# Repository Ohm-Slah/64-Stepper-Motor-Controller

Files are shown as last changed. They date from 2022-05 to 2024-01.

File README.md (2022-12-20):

# 64-Stepper-Motor-Controller
Controls an 8x8 array of stepper motors and RGB LED light strips, intended for audio/visual performance of a MIDI-like structure. You can certainly make this project with an FPGA, but I don't have much knowledge of FPGA's, so this project is written in C/C++ with the Arduino library included. Due to the incredible number of I/O, three Teensy microcontrollers are currently implemented, two Teensy 4.0's for I/O drivers (32 motors each), and one Teensy 4.1 for the 'main brain'. 

# Concetual initial design
General layout thoughts for such a large number of stepper motors and how to control them. Revision A is mostly based off of Concept #3.

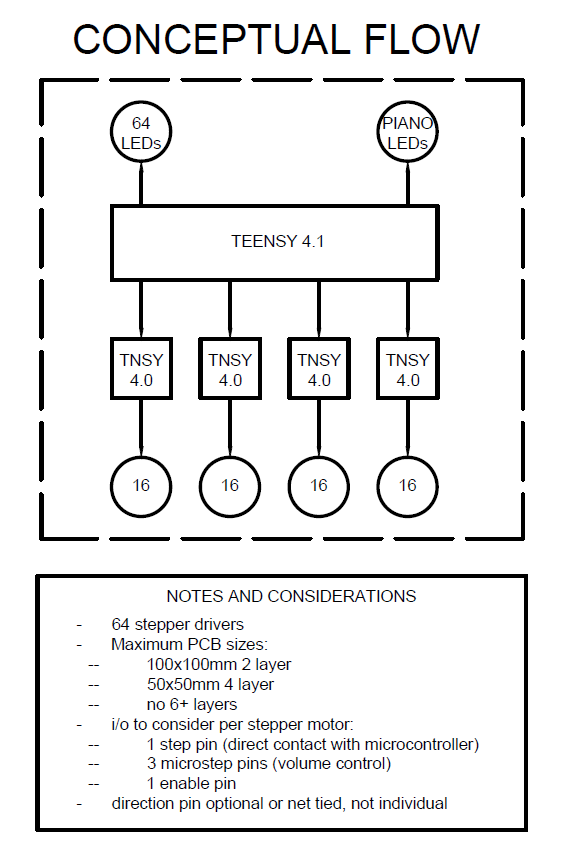
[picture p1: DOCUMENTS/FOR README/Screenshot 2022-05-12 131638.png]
conceptual
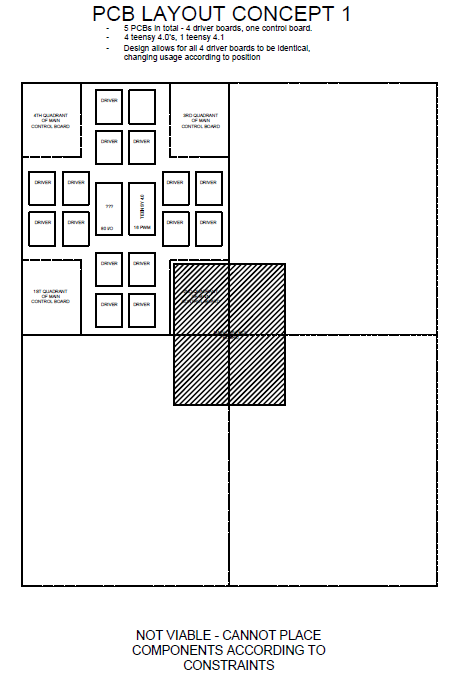
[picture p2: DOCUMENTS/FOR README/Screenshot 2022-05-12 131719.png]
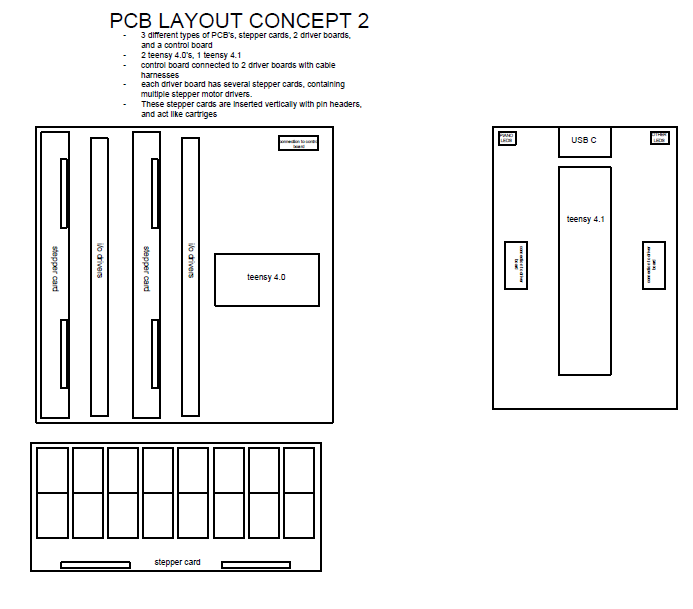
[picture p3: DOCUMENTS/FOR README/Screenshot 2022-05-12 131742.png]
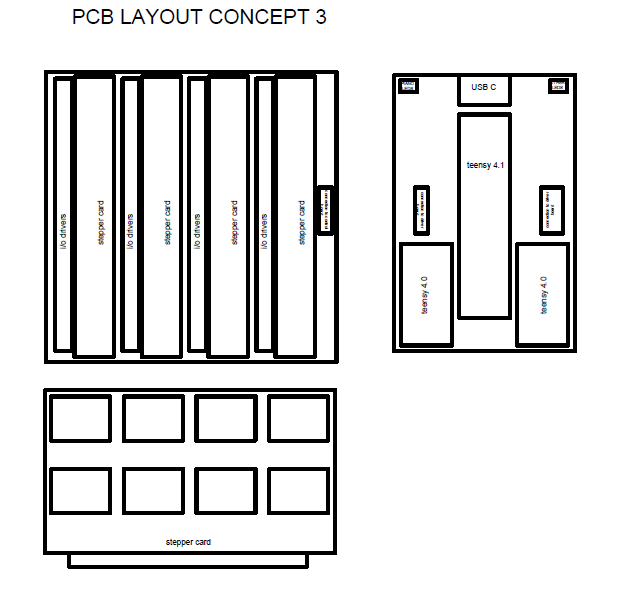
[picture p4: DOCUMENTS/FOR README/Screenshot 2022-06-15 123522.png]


# Revision A
This design is an attempt to create a fairly modular assembly for 64 stepper motor control. Each A4988 stepper driver can be extracted or replaced if neccessary. Eight total A4988 stepper drivers can be placed onto a single driver 'card'. These are designed to be edge-card connected to a larger board, the 32-stepper board. This board holds four driver cards, totalling to 32 stepper motors. There are 2 of these boards to total 64 motor drivers, with each having 20 74HC595 shift registers for I/O management, and visual indicator LED's for all outputs of the shift registers. Power is supplied to this board via a high-current connector. Both of these 32-stepper boards are then connected to a 'main board' containing the 3 microcontrollers, LED strip connections, and USB connection. 

## 8 Stepper PCB Card
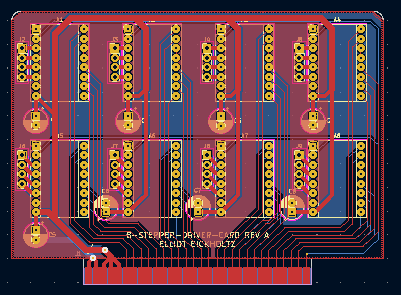
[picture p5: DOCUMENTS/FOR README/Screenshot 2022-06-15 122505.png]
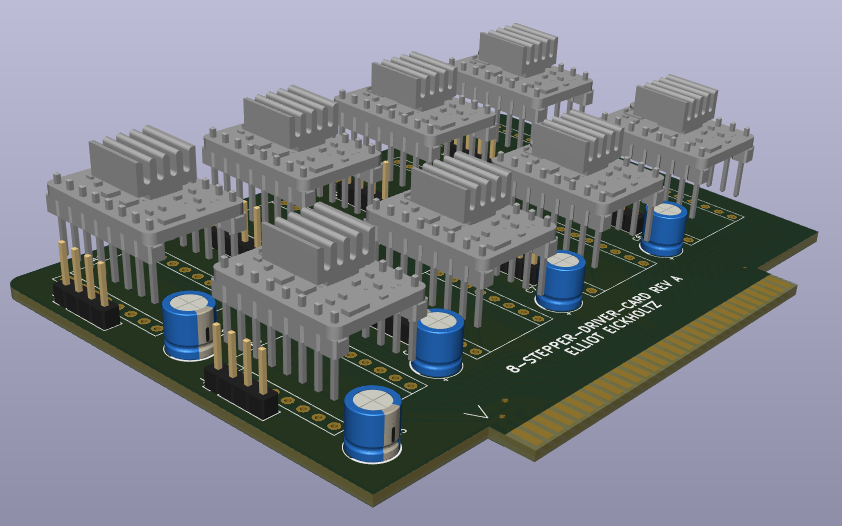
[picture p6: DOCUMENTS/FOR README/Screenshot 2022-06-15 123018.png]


## 32 Stepper PCB Board
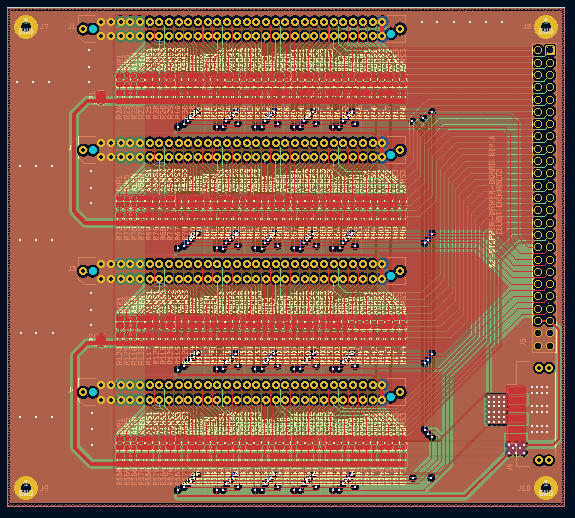
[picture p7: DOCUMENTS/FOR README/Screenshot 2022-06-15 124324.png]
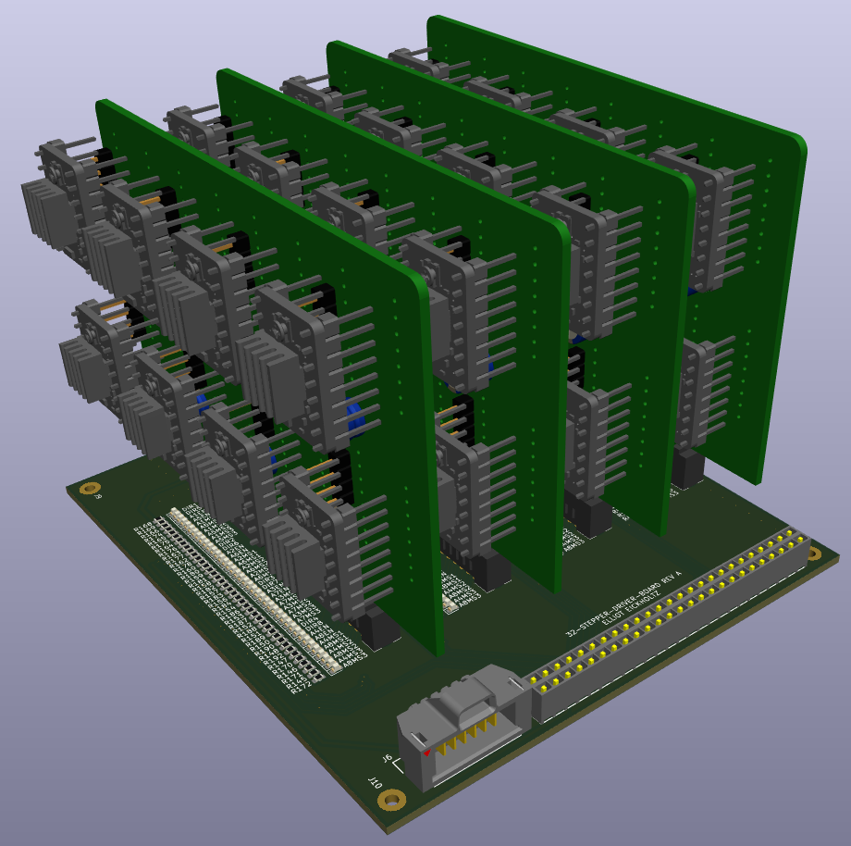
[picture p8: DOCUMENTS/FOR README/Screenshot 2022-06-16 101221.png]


## 64 Stepper PCB Board
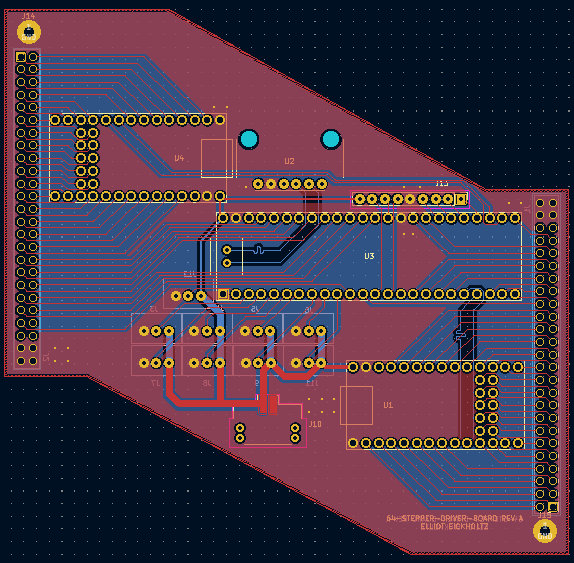
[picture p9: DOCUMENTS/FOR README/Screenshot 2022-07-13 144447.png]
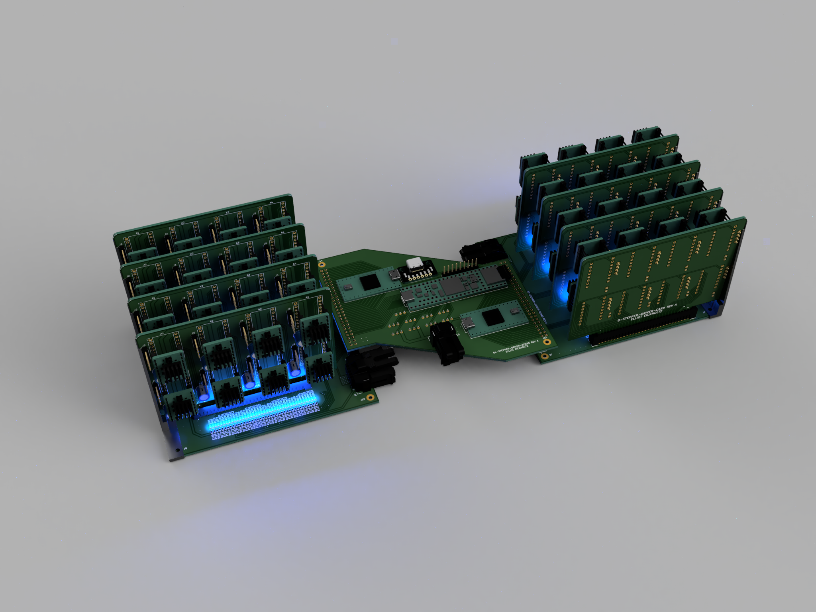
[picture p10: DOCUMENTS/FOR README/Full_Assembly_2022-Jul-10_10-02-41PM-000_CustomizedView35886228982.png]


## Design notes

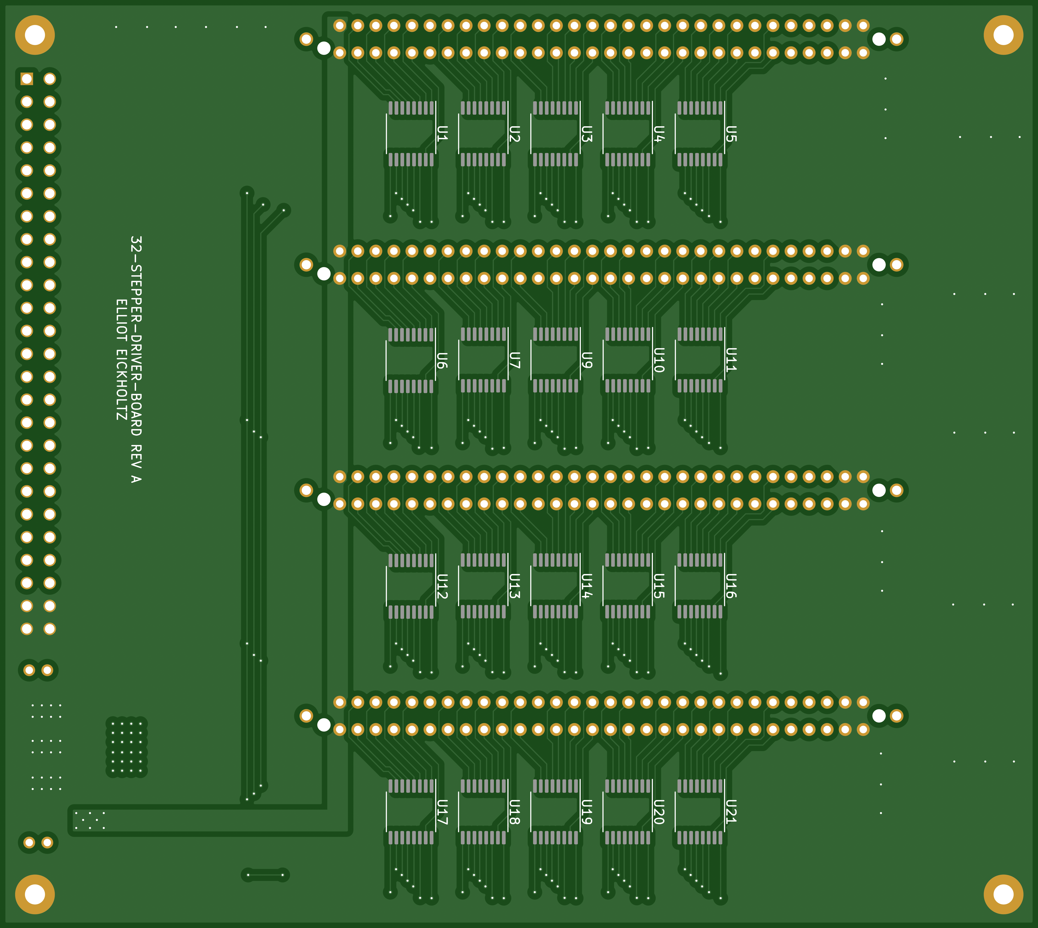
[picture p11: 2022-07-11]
PCB/32-STEPPER-DRIVER-BOARD/SVG/bottom.png

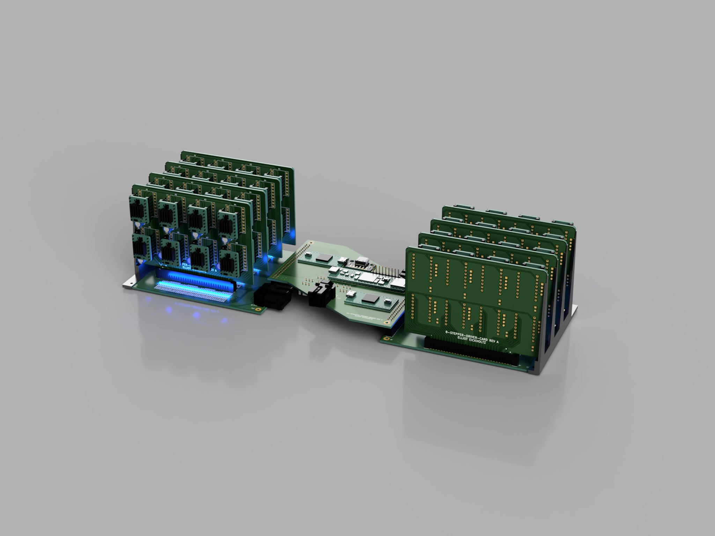
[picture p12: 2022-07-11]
PCB/64-STEPPER-CONTROLLER/32635d5f-a620-4e4e-a5b7-3e85a7bd913b.PNG

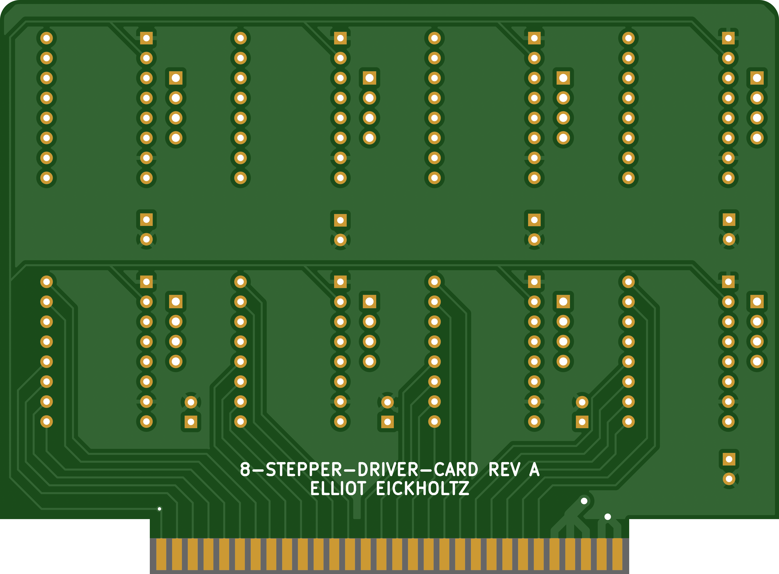
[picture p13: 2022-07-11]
PCB/8-STEPPER-DRIVER-CARD/SVG/BOTTOM.png

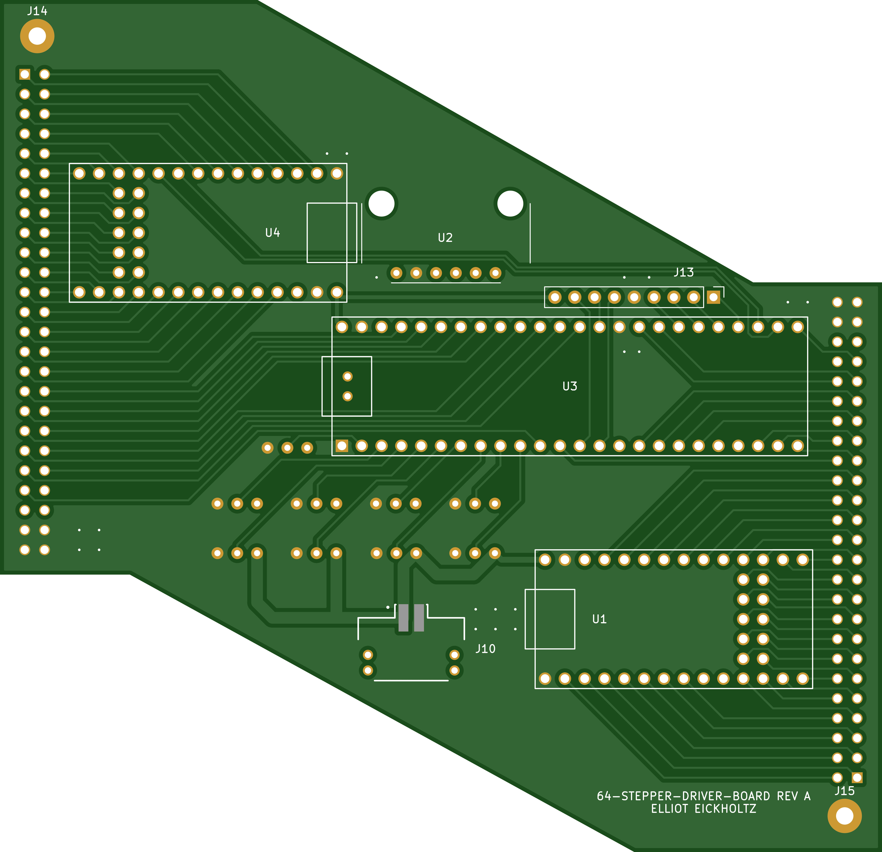
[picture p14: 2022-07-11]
PCB/64-STEPPER-CONTROLLER/SVG/TOP.png

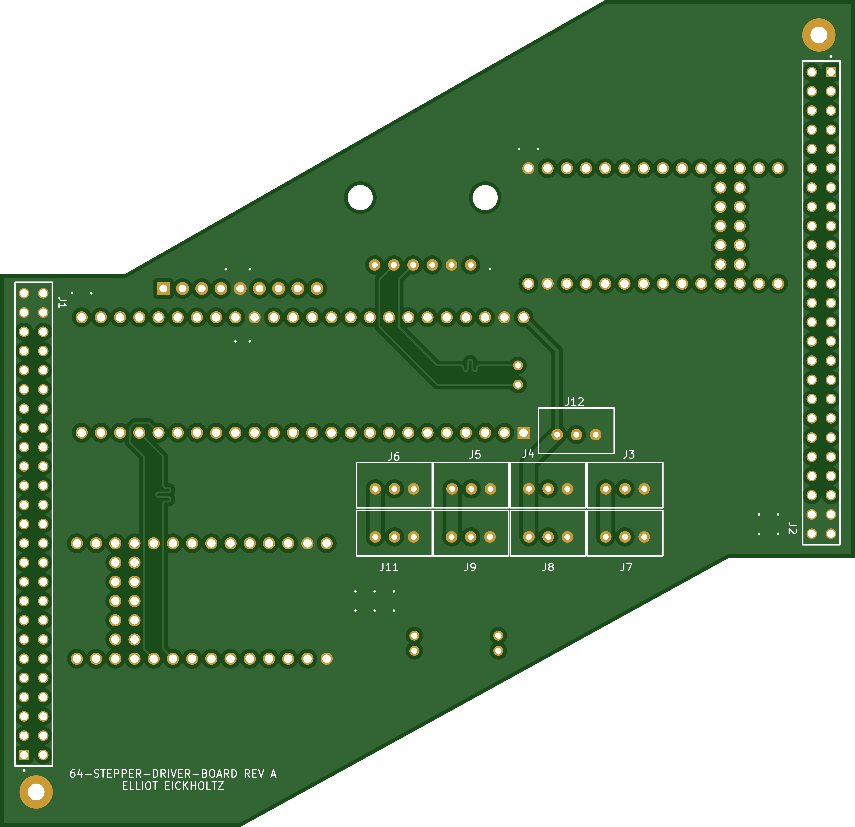
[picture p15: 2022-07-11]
PCB/64-STEPPER-CONTROLLER/SVG/BOTTOM.png

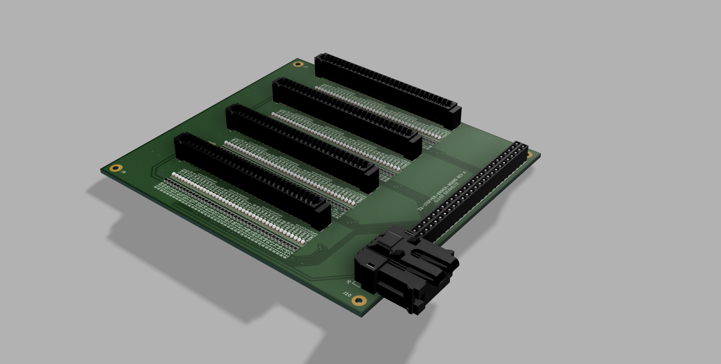
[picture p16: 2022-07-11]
PCB/64-STEPPER-CONTROLLER/32-STEPPER-DRIVER-BOARD v6.png

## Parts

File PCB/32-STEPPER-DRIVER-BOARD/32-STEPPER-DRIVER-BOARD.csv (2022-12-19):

Source: | C:\Users\34892\OneDrive - Samtec\Documents\GitHub\64-Stepper-Motor-Controller\PCB\32-STEPPER-DRIVER-BOARD\32-STEPPER-DRIVER-BOARD.kicad_sch
Date: | 12/19/2022 12:13:00 PM
Tool: | Eeschema (6.0.7)
Generator: | C:\Program Files\KiCad\6.0\bin\scripting\plugins/bom_csv_grouped_by_value.py
Component Count: | 352
Individual Components:
Item | Qty | Reference(s) | Value | LibPart | Footprint | Datasheet | MANUFACTURER | MAXIMUM_PACKAGE_HEIGHT | PARTREV | STANDARD | manf#
 |  | D1 | LED | Device:LED | LED_SMD:LED_0603_1608Metric | ~ |  |  |  |  | B1931NB--20C007614U1930
 |  | D2 | LED | Device:LED | LED_SMD:LED_0603_1608Metric | ~ |  |  |  |  | B1931NB--20C007614U1930
 |  | D3 | LED | Device:LED | LED_SMD:LED_0603_1608Metric | ~ |  |  |  |  | B1931NB--20C007614U1930
 |  | D4 | LED | Device:LED | LED_SMD:LED_0603_1608Metric | ~ |  |  |  |  | B1931NB--20C007614U1930
 |  | D6 | LED | Device:LED | LED_SMD:LED_0603_1608Metric | ~ |  |  |  |  | B1931NB--20C007614U1930
 |  | D7 | LED | Device:LED | LED_SMD:LED_0603_1608Metric | ~ |  |  |  |  | B1931NB--20C007614U1930
 |  | D8 | LED | Device:LED | LED_SMD:LED_0603_1608Metric | ~ |  |  |  |  | B1931NB--20C007614U1930
 |  | D9 | LED | Device:LED | LED_SMD:LED_0603_1608Metric | ~ |  |  |  |  | B1931NB--20C007614U1930
 |  | D10 | LED | Device:LED | LED_SMD:LED_0603_1608Metric | ~ |  |  |  |  | B1931NB--20C007614U1930
 |  | D12 | LED | Device:LED | LED_SMD:LED_0603_1608Metric | ~ |  |  |  |  | B1931NB--20C007614U1930
 |  | D13 | LED | Device:LED | LED_SMD:LED_0603_1608Metric | ~ |  |  |  |  | B1931NB--20C007614U1930
 |  | D14 | LED | Device:LED | LED_SMD:LED_0603_1608Metric | ~ |  |  |  |  | B1931NB--20C007614U1930
 |  | D15 | LED | Device:LED | LED_SMD:LED_0603_1608Metric | ~ |  |  |  |  | B1931NB--20C007614U1930
 |  | D16 | LED | Device:LED | LED_SMD:LED_0603_1608Metric | ~ |  |  |  |  | B1931NB--20C007614U1930
 |  | D18 | LED | Device:LED | LED_SMD:LED_0603_1608Metric | ~ |  |  |  |  | B1931NB--20C007614U1930
 |  | D19 | LED | Device:LED | LED_SMD:LED_0603_1608Metric | ~ |  |  |  |  | B1931NB--20C007614U1930
 |  | D20 | LED | Device:LED | LED_SMD:LED_0603_1608Metric | ~ |  |  |  |  | B1931NB--20C007614U1930
 |  | D21 | LED | Device:LED | LED_SMD:LED_0603_1608Metric | ~ |  |  |  |  | B1931NB--20C007614U1930
 |  | D22 | LED | Device:LED | LED_SMD:LED_0603_1608Metric | ~ |  |  |  |  | B1931NB--20C007614U1930
 |  | D24 | LED | Device:LED | LED_SMD:LED_0603_1608Metric | ~ |  |  |  |  | B1931NB--20C007614U1930
 |  | D25 | LED | Device:LED | LED_SMD:LED_0603_1608Metric | ~ |  |  |  |  | B1931NB--20C007614U1930
 |  | D27 | LED | Device:LED | LED_SMD:LED_0603_1608Metric | ~ |  |  |  |  | B1931NB--20C007614U1930
 |  | D28 | LED | Device:LED | LED_SMD:LED_0603_1608Metric | ~ |  |  |  |  | B1931NB--20C007614U1930
 |  | D29 | LED | Device:LED | LED_SMD:LED_0603_1608Metric | ~ |  |  |  |  | B1931NB--20C007614U1930
 |  | D30 | LED | Device:LED | LED_SMD:LED_0603_1608Metric | ~ |  |  |  |  | B1931NB--20C007614U1930
 |  | D31 | LED | Device:LED | LED_SMD:LED_0603_1608Metric | ~ |  |  |  |  | B1931NB--20C007614U1930
 |  | D33 | LED | Device:LED | LED_SMD:LED_0603_1608Metric | ~ |  |  |  |  | B1931NB--20C007614U1930
 |  | D34 | LED | Device:LED | LED_SMD:LED_0603_1608Metric | ~ |  |  |  |  | B1931NB--20C007614U1930
 |  | D35 | LED | Device:LED | LED_SMD:LED_0603_1608Metric | ~ |  |  |  |  | B1931NB--20C007614U1930
 |  | D36 | LED | Device:LED | LED_SMD:LED_0603_1608Metric | ~ |  |  |  |  | B1931NB--20C007614U1930
 |  | D37 | LED | Device:LED | LED_SMD:LED_0603_1608Metric | ~ |  |  |  |  | B1931NB--20C007614U1930
 |  | D39 | LED | Device:LED | LED_SMD:LED_0603_1608Metric | ~ |  |  |  |  | B1931NB--20C007614U1930
 |  | D40 | LED | Device:LED | LED_SMD:LED_0603_1608Metric | ~ |  |  |  |  | B1931NB--20C007614U1930
 |  | D41 | LED | Device:LED | LED_SMD:LED_0603_1608Metric | ~ |  |  |  |  | B1931NB--20C007614U1930
 |  | D42 | LED | Device:LED | LED_SMD:LED_0603_1608Metric | ~ |  |  |  |  | B1931NB--20C007614U1930
 |  | D43 | LED | Device:LED | LED_SMD:LED_0603_1608Metric | ~ |  |  |  |  | B1931NB--20C007614U1930
 |  | D45 | LED | Device:LED | LED_SMD:LED_0603_1608Metric | ~ |  |  |  |  | B1931NB--20C007614U1930
 |  | D46 | LED | Device:LED | LED_SMD:LED_0603_1608Metric | ~ |  |  |  |  | B1931NB--20C007614U1930
 |  | D47 | LED | Device:LED | LED_SMD:LED_0603_1608Metric | ~ |  |  |  |  | B1931NB--20C007614U1930
 |  | D48 | LED | Device:LED | LED_SMD:LED_0603_1608Metric | ~ |  |  |  |  | B1931NB--20C007614U1930
 |  | D49 | LED | Device:LED | LED_SMD:LED_0603_1608Metric | ~ |  |  |  |  | B1931NB--20C007614U1930
 |  | D50 | LED | Device:LED | LED_SMD:LED_0603_1608Metric | ~ |  |  |  |  | B1931NB--20C007614U1930
 |  | D51 | LED | Device:LED | LED_SMD:LED_0603_1608Metric | ~ |  |  |  |  | B1931NB--20C007614U1930
 |  | D52 | LED | Device:LED | LED_SMD:LED_0603_1608Metric | ~ |  |  |  |  | B1931NB--20C007614U1930
 |  | D54 | LED | Device:LED | LED_SMD:LED_0603_1608Metric | ~ |  |  |  |  | B1931NB--20C007614U1930
 |  | D55 | LED | Device:LED | LED_SMD:LED_0603_1608Metric | ~ |  |  |  |  | B1931NB--20C007614U1930
 |  | D56 | LED | Device:LED | LED_SMD:LED_0603_1608Metric | ~ |  |  |  |  | B1931NB--20C007614U1930
 |  | D57 | LED | Device:LED | LED_SMD:LED_0603_1608Metric | ~ |  |  |  |  | B1931NB--20C007614U1930
 |  | D58 | LED | Device:LED | LED_SMD:LED_0603_1608Metric | ~ |  |  |  |  | B1931NB--20C007614U1930
 |  | D60 | LED | Device:LED | LED_SMD:LED_0603_1608Metric | ~ |  |  |  |  | B1931NB--20C007614U1930
 |  | D61 | LED | Device:LED | LED_SMD:LED_0603_1608Metric | ~ |  |  |  |  | B1931NB--20C007614U1930
 |  | D62 | LED | Device:LED | LED_SMD:LED_0603_1608Metric | ~ |  |  |  |  | B1931NB--20C007614U1930
 |  | D63 | LED | Device:LED | LED_SMD:LED_0603_1608Metric | ~ |  |  |  |  | B1931NB--20C007614U1930
 |  | D64 | LED | Device:LED | LED_SMD:LED_0603_1608Metric | ~ |  |  |  |  | B1931NB--20C007614U1930
 |  | D66 | LED | Device:LED | LED_SMD:LED_0603_1608Metric | ~ |  |  |  |  | B1931NB--20C007614U1930
 |  | D67 | LED | Device:LED | LED_SMD:LED_0603_1608Metric | ~ |  |  |  |  | B1931NB--20C007614U1930
 |  | D68 | LED | Device:LED | LED_SMD:LED_0603_1608Metric | ~ |  |  |  |  | B1931NB--20C007614U1930
 |  | D69 | LED | Device:LED | LED_SMD:LED_0603_1608Metric | ~ |  |  |  |  | B1931NB--20C007614U1930
 |  | D70 | LED | Device:LED | LED_SMD:LED_0603_1608Metric | ~ |  |  |  |  | B1931NB--20C007614U1930
 |  | D72 | LED | Device:LED | LED_SMD:LED_0603_1608Metric | ~ |  |  |  |  | B1931NB--20C007614U1930
 |  | D73 | LED | Device:LED | LED_SMD:LED_0603_1608Metric | ~ |  |  |  |  | B1931NB--20C007614U1930
 |  | D75 | LED | Device:LED | LED_SMD:LED_0603_1608Metric | ~ |  |  |  |  | B1931NB--20C007614U1930
 |  | D76 | LED | Device:LED | LED_SMD:LED_0603_1608Metric | ~ |  |  |  |  | B1931NB--20C007614U1930
 |  | D77 | LED | Device:LED | LED_SMD:LED_0603_1608Metric | ~ |  |  |  |  | B1931NB--20C007614U1930
 |  | D78 | LED | Device:LED | LED_SMD:LED_0603_1608Metric | ~ |  |  |  |  | B1931NB--20C007614U1930
 |  | D79 | LED | Device:LED | LED_SMD:LED_0603_1608Metric | ~ |  |  |  |  | B1931NB--20C007614U1930
 |  | D81 | LED | Device:LED | LED_SMD:LED_0603_1608Metric | ~ |  |  |  |  | B1931NB--20C007614U1930
 |  | D82 | LED | Device:LED | LED_SMD:LED_0603_1608Metric | ~ |  |  |  |  | B1931NB--20C007614U1930
 |  | D83 | LED | Device:LED | LED_SMD:LED_0603_1608Metric | ~ |  |  |  |  | B1931NB--20C007614U1930
 |  | D84 | LED | Device:LED | LED_SMD:LED_0603_1608Metric | ~ |  |  |  |  | B1931NB--20C007614U1930
 |  | D85 | LED | Device:LED | LED_SMD:LED_0603_1608Metric | ~ |  |  |  |  | B1931NB--20C007614U1930
 |  | D87 | LED | Device:LED | LED_SMD:LED_0603_1608Metric | ~ |  |  |  |  | B1931NB--20C007614U1930
 |  | D88 | LED | Device:LED | LED_SMD:LED_0603_1608Metric | ~ |  |  |  |  | B1931NB--20C007614U1930
 |  | D89 | LED | Device:LED | LED_SMD:LED_0603_1608Metric | ~ |  |  |  |  | B1931NB--20C007614U1930
 |  | D90 | LED | Device:LED | LED_SMD:LED_0603_1608Metric | ~ |  |  |  |  | B1931NB--20C007614U1930
 |  | D91 | LED | Device:LED | LED_SMD:LED_0603_1608Metric | ~ |  |  |  |  | B1931NB--20C007614U1930
 |  | D93 | LED | Device:LED | LED_SMD:LED_0603_1608Metric | ~ |  |  |  |  | B1931NB--20C007614U1930
 |  | D94 | LED | Device:LED | LED_SMD:LED_0603_1608Metric | ~ |  |  |  |  | B1931NB--20C007614U1930
 |  | D95 | LED | Device:LED | LED_SMD:LED_0603_1608Metric | ~ |  |  |  |  | B1931NB--20C007614U1930
 |  | D96 | LED | Device:LED | LED_SMD:LED_0603_1608Metric | ~ |  |  |  |  | B1931NB--20C007614U1930
 |  | D97 | LED | Device:LED | LED_SMD:LED_0603_1608Metric | ~ |  |  |  |  | B1931NB--20C007614U1930
 |  | D98 | LED | Device:LED | LED_SMD:LED_0603_1608Metric | ~ |  |  |  |  | B1931NB--20C007614U1930
 |  | D99 | LED | Device:LED | LED_SMD:LED_0603_1608Metric | ~ |  |  |  |  | B1931NB--20C007614U1930
 |  | D100 | LED | Device:LED | LED_SMD:LED_0603_1608Metric | ~ |  |  |  |  | B1931NB--20C007614U1930
 |  | D102 | LED | Device:LED | LED_SMD:LED_0603_1608Metric | ~ |  |  |  |  | B1931NB--20C007614U1930
 |  | D103 | LED | Device:LED | LED_SMD:LED_0603_1608Metric | ~ |  |  |  |  | B1931NB--20C007614U1930
 |  | D104 | LED | Device:LED | LED_SMD:LED_0603_1608Metric | ~ |  |  |  |  | B1931NB--20C007614U1930
 |  | D105 | LED | Device:LED | LED_SMD:LED_0603_1608Metric | ~ |  |  |  |  | B1931NB--20C007614U1930
 |  | D106 | LED | Device:LED | LED_SMD:LED_0603_1608Metric | ~ |  |  |  |  | B1931NB--20C007614U1930
 |  | D108 | LED | Device:LED | LED_SMD:LED_0603_1608Metric | ~ |  |  |  |  | B1931NB--20C007614U1930
 |  | D109 | LED | Device:LED | LED_SMD:LED_0603_1608Metric | ~ |  |  |  |  | B1931NB--20C007614U1930
 |  | D110 | LED | Device:LED | LED_SMD:LED_0603_1608Metric | ~ |  |  |  |  | B1931NB--20C007614U1930
 |  | D111 | LED | Device:LED | LED_SMD:LED_0603_1608Metric | ~ |  |  |  |  | B1931NB--20C007614U1930
 |  | D112 | LED | Device:LED | LED_SMD:LED_0603_1608Metric | ~ |  |  |  |  | B1931NB--20C007614U1930
 |  | D114 | LED | Device:LED | LED_SMD:LED_0603_1608Metric | ~ |  |  |  |  | B1931NB--20C007614U1930
 |  | D115 | LED | Device:LED | LED_SMD:LED_0603_1608Metric | ~ |  |  |  |  | B1931NB--20C007614U1930
 |  | D116 | LED | Device:LED | LED_SMD:LED_0603_1608Metric | ~ |  |  |  |  | B1931NB--20C007614U1930
 |  | D117 | LED | Device:LED | LED_SMD:LED_0603_1608Metric | ~ |  |  |  |  | B1931NB--20C007614U1930
 |  | D118 | LED | Device:LED | LED_SMD:LED_0603_1608Metric | ~ |  |  |  |  | B1931NB--20C007614U1930
 |  | D120 | LED | Device:LED | LED_SMD:LED_0603_1608Metric | ~ |  |  |  |  | B1931NB--20C007614U1930
 |  | D121 | LED | Device:LED | LED_SMD:LED_0603_1608Metric | ~ |  |  |  |  | B1931NB--20C007614U1930
 |  | D123 | LED | Device:LED | LED_SMD:LED_0603_1608Metric | ~ |  |  |  |  | B1931NB--20C007614U1930
 |  | D124 | LED | Device:LED | LED_SMD:LED_0603_1608Metric | ~ |  |  |  |  | B1931NB--20C007614U1930
 |  | D125 | LED | Device:LED | LED_SMD:LED_0603_1608Metric | ~ |  |  |  |  | B1931NB--20C007614U1930
 |  | D126 | LED | Device:LED | LED_SMD:LED_0603_1608Metric | ~ |  |  |  |  | B1931NB--20C007614U1930
 |  | D127 | LED | Device:LED | LED_SMD:LED_0603_1608Metric | ~ |  |  |  |  | B1931NB--20C007614U1930
 |  | D129 | LED | Device:LED | LED_SMD:LED_0603_1608Metric | ~ |  |  |  |  | B1931NB--20C007614U1930
 |  | D130 | LED | Device:LED | LED_SMD:LED_0603_1608Metric | ~ |  |  |  |  | B1931NB--20C007614U1930
 |  | D131 | LED | Device:LED | LED_SMD:LED_0603_1608Metric | ~ |  |  |  |  | B1931NB--20C007614U1930
 |  | D132 | LED | Device:LED | LED_SMD:LED_0603_1608Metric | ~ |  |  |  |  | B1931NB--20C007614U1930
 |  | D133 | LED | Device:LED | LED_SMD:LED_0603_1608Metric | ~ |  |  |  |  | B1931NB--20C007614U1930
 |  | D135 | LED | Device:LED | LED_SMD:LED_0603_1608Metric | ~ |  |  |  |  | B1931NB--20C007614U1930
 |  | D136 | LED | Device:LED | LED_SMD:LED_0603_1608Metric | ~ |  |  |  |  | B1931NB--20C007614U1930
 |  | D137 | LED | Device:LED | LED_SMD:LED_0603_1608Metric | ~ |  |  |  |  | B1931NB--20C007614U1930
 |  | D138 | LED | Device:LED | LED_SMD:LED_0603_1608Metric | ~ |  |  |  |  | B1931NB--20C007614U1930
 |  | D139 | LED | Device:LED | LED_SMD:LED_0603_1608Metric | ~ |  |  |  |  | B1931NB--20C007614U1930
 |  | D141 | LED | Device:LED | LED_SMD:LED_0603_1608Metric | ~ |  |  |  |  | B1931NB--20C007614U1930
 |  | D142 | LED | Device:LED | LED_SMD:LED_0603_1608Metric | ~ |  |  |  |  | B1931NB--20C007614U1930
 |  | D143 | LED | Device:LED | LED_SMD:LED_0603_1608Metric | ~ |  |  |  |  | B1931NB--20C007614U1930
 |  | D144 | LED | Device:LED | LED_SMD:LED_0603_1608Metric | ~ |  |  |  |  | B1931NB--20C007614U1930
 |  | D145 | LED | Device:LED | LED_SMD:LED_0603_1608Metric | ~ |  |  |  |  | B1931NB--20C007614U1930
 |  | D146 | LED | Device:LED | LED_SMD:LED_0603_1608Metric | ~ |  |  |  |  | B1931NB--20C007614U1930
 |  | D147 | LED | Device:LED | LED_SMD:LED_0603_1608Metric | ~ |  |  |  |  | B1931NB--20C007614U1930
 |  | D148 | LED | Device:LED | LED_SMD:LED_0603_1608Metric | ~ |  |  |  |  | B1931NB--20C007614U1930
 |  | D150 | LED | Device:LED | LED_SMD:LED_0603_1608Metric | ~ |  |  |  |  | B1931NB--20C007614U1930
 |  | D151 | LED | Device:LED | LED_SMD:LED_0603_1608Metric | ~ |  |  |  |  | B1931NB--20C007614U1930
 |  | D152 | LED | Device:LED | LED_SMD:LED_0603_1608Metric | ~ |  |  |  |  | B1931NB--20C007614U1930
 |  | D153 | LED | Device:LED | LED_SMD:LED_0603_1608Metric | ~ |  |  |  |  | B1931NB--20C007614U1930
 |  | D154 | LED | Device:LED | LED_SMD:LED_0603_1608Metric | ~ |  |  |  |  | B1931NB--20C007614U1930
 |  | D156 | LED | Device:LED | LED_SMD:LED_0603_1608Metric | ~ |  |  |  |  | B1931NB--20C007614U1930
 |  | D157 | LED | Device:LED | LED_SMD:LED_0603_1608Metric | ~ |  |  |  |  | B1931NB--20C007614U1930
 |  | D158 | LED | Device:LED | LED_SMD:LED_0603_1608Metric | ~ |  |  |  |  | B1931NB--20C007614U1930
 |  | D159 | LED | Device:LED | LED_SMD:LED_0603_1608Metric | ~ |  |  |  |  | B1931NB--20C007614U1930
 |  | D160 | LED | Device:LED | LED_SMD:LED_0603_1608Metric | ~ |  |  |  |  | B1931NB--20C007614U1930
 |  | D162 | LED | Device:LED | LED_SMD:LED_0603_1608Metric | ~ |  |  |  |  | B1931NB--20C007614U1930
 |  | D163 | LED | Device:LED | LED_SMD:LED_0603_1608Metric | ~ |  |  |  |  | B1931NB--20C007614U1930
 |  | D164 | LED | Device:LED | LED_SMD:LED_0603_1608Metric | ~ |  |  |  |  | B1931NB--20C007614U1930
 |  | D165 | LED | Device:LED | LED_SMD:LED_0603_1608Metric | ~ |  |  |  |  | B1931NB--20C007614U1930
 |  | D166 | LED | Device:LED | LED_SMD:LED_0603_1608Metric | ~ |  |  |  |  | B1931NB--20C007614U1930
 |  | D168 | LED | Device:LED | LED_SMD:LED_0603_1608Metric | ~ |  |  |  |  | B1931NB--20C007614U1930
 |  | D169 | LED | Device:LED | LED_SMD:LED_0603_1608Metric | ~ |  |  |  |  | B1931NB--20C007614U1930
 |  | D170 | LED | Device:LED | LED_SMD:LED_0603_1608Metric | ~ |  |  |  |  | B1931NB--20C007614U1930
 |  | D171 | LED | Device:LED | LED_SMD:LED_0603_1608Metric | ~ |  |  |  |  | B1931NB--20C007614U1930
 |  | D172 | LED | Device:LED | LED_SMD:LED_0603_1608Metric | ~ |  |  |  |  | B1931NB--20C007614U1930
 |  | D174 | LED | Device:LED | LED_SMD:LED_0603_1608Metric | ~ |  |  |  |  | B1931NB--20C007614U1930
 |  | D175 | LED | Device:LED | LED_SMD:LED_0603_1608Metric | ~ |  |  |  |  | B1931NB--20C007614U1930
 |  | D176 | LED | Device:LED | LED_SMD:LED_0603_1608Metric | ~ |  |  |  |  | B1931NB--20C007614U1930
 |  | D177 | LED | Device:LED | LED_SMD:LED_0603_1608Metric | ~ |  |  |  |  | B1931NB--20C007614U1930
 |  | D178 | LED | Device:LED | LED_SMD:LED_0603_1608Metric | ~ |  |  |  |  | B1931NB--20C007614U1930
 |  | D180 | LED | Device:LED | LED_SMD:LED_0603_1608Metric | ~ |  |  |  |  | B1931NB--20C007614U1930
 |  | D181 | LED | Device:LED | LED_SMD:LED_0603_1608Metric | ~ |  |  |  |  | B1931NB--20C007614U1930
 |  | D182 | LED | Device:LED | LED_SMD:LED_0603_1608Metric | ~ |  |  |  |  | B1931NB--20C007614U1930
 |  | D183 | LED | Device:LED | LED_SMD:LED_0603_1608Metric | ~ |  |  |  |  | B1931NB--20C007614U1930
 |  | D184 | LED | Device:LED | LED_SMD:LED_0603_1608Metric | ~ |  |  |  |  | B1931NB--20C007614U1930
 |  | D186 | LED | Device:LED | LED_SMD:LED_0603_1608Metric | ~ |  |  |  |  | B1931NB--20C007614U1930
 |  | D187 | LED | Device:LED | LED_SMD:LED_0603_1608Metric | ~ |  |  |  |  | B1931NB--20C007614U1930
 |  | D188 | LED | Device:LED | LED_SMD:LED_0603_1608Metric | ~ |  |  |  |  | B1931NB--20C007614U1930
 |  | D189 | LED | Device:LED | LED_SMD:LED_0603_1608Metric | ~ |  |  |  |  | B1931NB--20C007614U1930
 |  | D190 | LED | Device:LED | LED_SMD:LED_0603_1608Metric | ~ |  |  |  |  | B1931NB--20C007614U1930
 |  | D192 | LED | Device:LED | LED_SMD:LED_0603_1608Metric | ~ |  |  |  |  | B1931NB--20C007614U1930
 |  | J1 | MEC2-30-01-X-TH1-NP-WT | MEC2-30-01-X-TH1-NP-WT:MEC2-30-01-X-TH1-NP-WT | LIBRARIES:SAMTEC_MEC2-30-01-X-TH1-NP-WT |  | Samtec | 8.75 mm | F | Manufacturer Recommendations | MEC2-30-01-L-TH1-NP-WT
 |  | J2 | MEC2-30-01-X-TH1-NP-WT | MEC2-30-01-X-TH1-NP-WT:MEC2-30-01-X-TH1-NP-WT | LIBRARIES:SAMTEC_MEC2-30-01-X-TH1-NP-WT |  | Samtec | 8.75 mm | F | Manufacturer Recommendations | MEC2-30-01-L-TH1-NP-WT
 |  | J3 | MEC2-30-01-X-TH1-NP-WT | MEC2-30-01-X-TH1-NP-WT:MEC2-30-01-X-TH1-NP-WT | LIBRARIES:SAMTEC_MEC2-30-01-X-TH1-NP-WT |  | Samtec | 8.75 mm | F | Manufacturer Recommendations | MEC2-30-01-L-TH1-NP-WT
 |  | J4 | MEC2-30-01-X-TH1-NP-WT | MEC2-30-01-X-TH1-NP-WT:MEC2-30-01-X-TH1-NP-WT | LIBRARIES:SAMTEC_MEC2-30-01-X-TH1-NP-WT |  | Samtec | 8.75 mm | F | Manufacturer Recommendations | MEC2-30-01-L-TH1-NP-WT
 |  | J5 | IPS1-125-01-S-D | IPS1-125-01-S-D:IPS1-125-01-S-D | LIBRARIES:SAMTEC_IPS1-125-01-S-D |  | Samtec |  | R | Manufacturer Recommendations | IPT1-125-01-S-D
 |  | J6 | UMPT-06-01-X-RA-WT-P-X | UMPT-06-01-X-RA-WT-P-X:UMPT-06-01-X-RA-WT-P-X | LIBRARIES:SAMTEC_UMPT-06-01-X-RA-WT-P-X |  | Samtec | 13.35 mm | 4 | Manufacturer Recommendations | UMPT-06-01-L-RA-WT-P-TR
 |  | J7 | Screw_Terminal_01x01 | Connector:Screw_Terminal_01x01 | MountingHole:MountingHole_2.2mm_M2_Pad | ~
 |  | J8 | Screw_Terminal_01x01 | Connector:Screw_Terminal_01x01 | MountingHole:MountingHole_2.2mm_M2_Pad | ~
 |  | J9 | Screw_Terminal_01x01 | Connector:Screw_Terminal_01x01 | MountingHole:MountingHole_2.2mm_M2_Pad | ~
 |  | J10 | Screw_Terminal_01x01 | Connector:Screw_Terminal_01x01 | MountingHole:MountingHole_2.2mm_M2_Pad | ~
 |  | JP1 | SolderJumper_2_Open | Jumper:SolderJumper_2_Open | Jumper:SolderJumper-2_P1.3mm_Open_RoundedPad1.0x1.5mm | ~
 |  | JP2 | SolderJumper_2_Open | Jumper:SolderJumper_2_Open | Jumper:SolderJumper-2_P1.3mm_Open_RoundedPad1.0x1.5mm | ~
 |  | R1 | R | Device:R | Resistor_SMD:R_0603_1608Metric | ~ |  |  |  |  | RC0603FR-071KL
 |  | R2 | R | Device:R | Resistor_SMD:R_0603_1608Metric | ~ |  |  |  |  | RC0603FR-071KL
 |  | R3 | R | Device:R | Resistor_SMD:R_0603_1608Metric | ~ |  |  |  |  | RC0603FR-071KL
 |  | R4 | R | Device:R | Resistor_SMD:R_0603_1608Metric | ~ |  |  |  |  | RC0603FR-071KL
 |  | R6 | R | Device:R | Resistor_SMD:R_0603_1608Metric | ~ |  |  |  |  | RC0603FR-071KL
 |  | R7 | R | Device:R | Resistor_SMD:R_0603_1608Metric | ~ |  |  |  |  | RC0603FR-071KL
 |  | R8 | R | Device:R | Resistor_SMD:R_0603_1608Metric | ~ |  |  |  |  | RC0603FR-071KL
 |  | R9 | R | Device:R | Resistor_SMD:R_0603_1608Metric | ~ |  |  |  |  | RC0603FR-071KL
 |  | R10 | R | Device:R | Resistor_SMD:R_0603_1608Metric | ~ |  |  |  |  | RC0603FR-071KL
 |  | R12 | R | Device:R | Resistor_SMD:R_0603_1608Metric | ~ |  |  |  |  | RC0603FR-071KL
 |  | R13 | R | Device:R | Resistor_SMD:R_0603_1608Metric | ~ |  |  |  |  | RC0603FR-071KL
 |  | R14 | R | Device:R | Resistor_SMD:R_0603_1608Metric | ~ |  |  |  |  | RC0603FR-071KL
 |  | R15 | R | Device:R | Resistor_SMD:R_0603_1608Metric | ~ |  |  |  |  | RC0603FR-071KL
 |  | R16 | R | Device:R | Resistor_SMD:R_0603_1608Metric | ~ |  |  |  |  | RC0603FR-071KL
 |  | R18 | R | Device:R | Resistor_SMD:R_0603_1608Metric | ~ |  |  |  |  | RC0603FR-071KL
 |  | R19 | R | Device:R | Resistor_SMD:R_0603_1608Metric | ~ |  |  |  |  | RC0603FR-071KL
 |  | R20 | R | Device:R | Resistor_SMD:R_0603_1608Metric | ~ |  |  |  |  | RC0603FR-071KL
 |  | R21 | R | Device:R | Resistor_SMD:R_0603_1608Metric | ~ |  |  |  |  | RC0603FR-071KL
 |  | R22 | R | Device:R | Resistor_SMD:R_0603_1608Metric | ~ |  |  |  |  | RC0603FR-071KL
 |  | R24 | R | Device:R | Resistor_SMD:R_0603_1608Metric | ~ |  |  |  |  | RC0603FR-071KL
 |  | R25 | R | Device:R | Resistor_SMD:R_0603_1608Metric | ~ |  |  |  |  | RC0603FR-071KL
 |  | R27 | R | Device:R | Resistor_SMD:R_0603_1608Metric | ~ |  |  |  |  | RC0603FR-071KL
 |  | R28 | R | Device:R | Resistor_SMD:R_0603_1608Metric | ~ |  |  |  |  | RC0603FR-071KL
 |  | R29 | R | Device:R | Resistor_SMD:R_0603_1608Metric | ~ |  |  |  |  | RC0603FR-071KL
 |  | R30 | R | Device:R | Resistor_SMD:R_0603_1608Metric | ~ |  |  |  |  | RC0603FR-071KL
 |  | R31 | R | Device:R | Resistor_SMD:R_0603_1608Metric | ~ |  |  |  |  | RC0603FR-071KL
 |  | R33 | R | Device:R | Resistor_SMD:R_0603_1608Metric | ~ |  |  |  |  | RC0603FR-071KL
 |  | R34 | R | Device:R | Resistor_SMD:R_0603_1608Metric | ~ |  |  |  |  | RC0603FR-071KL
 |  | R35 | R | Device:R | Resistor_SMD:R_0603_1608Metric | ~ |  |  |  |  | RC0603FR-071KL
 |  | R36 | R | Device:R | Resistor_SMD:R_0603_1608Metric | ~ |  |  |  |  | RC0603FR-071KL
 |  | R37 | R | Device:R | Resistor_SMD:R_0603_1608Metric | ~ |  |  |  |  | RC0603FR-071KL
 |  | R39 | R | Device:R | Resistor_SMD:R_0603_1608Metric | ~ |  |  |  |  | RC0603FR-071KL
 |  | R40 | R | Device:R | Resistor_SMD:R_0603_1608Metric | ~ |  |  |  |  | RC0603FR-071KL
 |  | R41 | R | Device:R | Resistor_SMD:R_0603_1608Metric | ~ |  |  |  |  | RC0603FR-071KL
 |  | R42 | R | Device:R | Resistor_SMD:R_0603_1608Metric | ~ |  |  |  |  | RC0603FR-071KL
 |  | R43 | R | Device:R | Resistor_SMD:R_0603_1608Metric | ~ |  |  |  |  | RC0603FR-071KL
 |  | R45 | R | Device:R | Resistor_SMD:R_0603_1608Metric | ~ |  |  |  |  | RC0603FR-071KL
 |  | R46 | R | Device:R | Resistor_SMD:R_0603_1608Metric | ~ |  |  |  |  | RC0603FR-071KL
 |  | R47 | R | Device:R | Resistor_SMD:R_0603_1608Metric | ~ |  |  |  |  | RC0603FR-071KL
 |  | R48 | R | Device:R | Resistor_SMD:R_0603_1608Metric | ~ |  |  |  |  | RC0603FR-071KL
 |  | R49 | R | Device:R | Resistor_SMD:R_0603_1608Metric | ~ |  |  |  |  | RC0603FR-071KL
 |  | R50 | R | Device:R | Resistor_SMD:R_0603_1608Metric | ~ |  |  |  |  | RC0603FR-071KL
 |  | R51 | R | Device:R | Resistor_SMD:R_0603_1608Metric | ~ |  |  |  |  | RC0603FR-071KL
 |  | R52 | R | Device:R | Resistor_SMD:R_0603_1608Metric | ~ |  |  |  |  | RC0603FR-071KL
 |  | R54 | R | Device:R | Resistor_SMD:R_0603_1608Metric | ~ |  |  |  |  | RC0603FR-071KL
 |  | R55 | R | Device:R | Resistor_SMD:R_0603_1608Metric | ~ |  |  |  |  | RC0603FR-071KL
 |  | R56 | R | Device:R | Resistor_SMD:R_0603_1608Metric | ~ |  |  |  |  | RC0603FR-071KL
 |  | R57 | R | Device:R | Resistor_SMD:R_0603_1608Metric | ~ |  |  |  |  | RC0603FR-071KL
 |  | R58 | R | Device:R | Resistor_SMD:R_0603_1608Metric | ~ |  |  |  |  | RC0603FR-071KL
 |  | R60 | R | Device:R | Resistor_SMD:R_0603_1608Metric | ~ |  |  |  |  | RC0603FR-071KL
 |  | R61 | R | Device:R | Resistor_SMD:R_0603_1608Metric | ~ |  |  |  |  | RC0603FR-071KL
 |  | R62 | R | Device:R | Resistor_SMD:R_0603_1608Metric | ~ |  |  |  |  | RC0603FR-071KL
 |  | R63 | R | Device:R | Resistor_SMD:R_0603_1608Metric | ~ |  |  |  |  | RC0603FR-071KL
 |  | R64 | R | Device:R | Resistor_SMD:R_0603_1608Metric | ~ |  |  |  |  | RC0603FR-071KL
 |  | R66 | R | Device:R | Resistor_SMD:R_0603_1608Metric | ~ |  |  |  |  | RC0603FR-071KL
 |  | R67 | R | Device:R | Resistor_SMD:R_0603_1608Metric | ~ |  |  |  |  | RC0603FR-071KL
 |  | R68 | R | Device:R | Resistor_SMD:R_0603_1608Metric | ~ |  |  |  |  | RC0603FR-071KL
 |  | R69 | R | Device:R | Resistor_SMD:R_0603_1608Metric | ~ |  |  |  |  | RC0603FR-071KL
 |  | R70 | R | Device:R | Resistor_SMD:R_0603_1608Metric | ~ |  |  |  |  | RC0603FR-071KL
 |  | R72 | R | Device:R | Resistor_SMD:R_0603_1608Metric | ~ |  |  |  |  | RC0603FR-071KL
 |  | R73 | R | Device:R | Resistor_SMD:R_0603_1608Metric | ~ |  |  |  |  | RC0603FR-071KL
 |  | R75 | R | Device:R | Resistor_SMD:R_0603_1608Metric | ~ |  |  |  |  | RC0603FR-071KL
 |  | R76 | R | Device:R | Resistor_SMD:R_0603_1608Metric | ~ |  |  |  |  | RC0603FR-071KL
 |  | R77 | R | Device:R | Resistor_SMD:R_0603_1608Metric | ~ |  |  |  |  | RC0603FR-071KL
 |  | R78 | R | Device:R | Resistor_SMD:R_0603_1608Metric | ~ |  |  |  |  | RC0603FR-071KL
 |  | R79 | R | Device:R | Resistor_SMD:R_0603_1608Metric | ~ |  |  |  |  | RC0603FR-071KL
 |  | R81 | R | Device:R | Resistor_SMD:R_0603_1608Metric | ~ |  |  |  |  | RC0603FR-071KL
 |  | R82 | R | Device:R | Resistor_SMD:R_0603_1608Metric | ~ |  |  |  |  | RC0603FR-071KL
 |  | R83 | R | Device:R | Resistor_SMD:R_0603_1608Metric | ~ |  |  |  |  | RC0603FR-071KL
 |  | R84 | R | Device:R | Resistor_SMD:R_0603_1608Metric | ~ |  |  |  |  | RC0603FR-071KL
 |  | R85 | R | Device:R | Resistor_SMD:R_0603_1608Metric | ~ |  |  |  |  | RC0603FR-071KL
 |  | R87 | R | Device:R | Resistor_SMD:R_0603_1608Metric | ~ |  |  |  |  | RC0603FR-071KL
 |  | R88 | R | Device:R | Resistor_SMD:R_0603_1608Metric | ~ |  |  |  |  | RC0603FR-071KL
 |  | R89 | R | Device:R | Resistor_SMD:R_0603_1608Metric | ~ |  |  |  |  | RC0603FR-071KL
 |  | R90 | R | Device:R | Resistor_SMD:R_0603_1608Metric | ~ |  |  |  |  | RC0603FR-071KL
 |  | R91 | R | Device:R | Resistor_SMD:R_0603_1608Metric | ~ |  |  |  |  | RC0603FR-071KL
 |  | R93 | R | Device:R | Resistor_SMD:R_0603_1608Metric | ~ |  |  |  |  | RC0603FR-071KL
 |  | R94 | R | Device:R | Resistor_SMD:R_0603_1608Metric | ~ |  |  |  |  | RC0603FR-071KL
 |  | R95 | R | Device:R | Resistor_SMD:R_0603_1608Metric | ~ |  |  |  |  | RC0603FR-071KL
 |  | R96 | R | Device:R | Resistor_SMD:R_0603_1608Metric | ~ |  |  |  |  | RC0603FR-071KL
 |  | R97 | R | Device:R | Resistor_SMD:R_0603_1608Metric | ~ |  |  |  |  | RC0603FR-071KL
 |  | R98 | R | Device:R | Resistor_SMD:R_0603_1608Metric | ~ |  |  |  |  | RC0603FR-071KL
 |  | R99 | R | Device:R | Resistor_SMD:R_0603_1608Metric | ~ |  |  |  |  | RC0603FR-071KL
 |  | R100 | R | Device:R | Resistor_SMD:R_0603_1608Metric | ~ |  |  |  |  | RC0603FR-071KL
 |  | R102 | R | Device:R | Resistor_SMD:R_0603_1608Metric | ~ |  |  |  |  | RC0603FR-071KL
 |  | R103 | R | Device:R | Resistor_SMD:R_0603_1608Metric | ~ |  |  |  |  | RC0603FR-071KL
 |  | R104 | R | Device:R | Resistor_SMD:R_0603_1608Metric | ~ |  |  |  |  | RC0603FR-071KL
 |  | R105 | R | Device:R | Resistor_SMD:R_0603_1608Metric | ~ |  |  |  |  | RC0603FR-071KL
 |  | R106 | R | Device:R | Resistor_SMD:R_0603_1608Metric | ~ |  |  |  |  | RC0603FR-071KL
 |  | R108 | R | Device:R | Resistor_SMD:R_0603_1608Metric | ~ |  |  |  |  | RC0603FR-071KL
 |  | R109 | R | Device:R | Resistor_SMD:R_0603_1608Metric | ~ |  |  |  |  | RC0603FR-071KL
 |  | R110 | R | Device:R | Resistor_SMD:R_0603_1608Metric | ~ |  |  |  |  | RC0603FR-071KL
 |  | R111 | R | Device:R | Resistor_SMD:R_0603_1608Metric | ~ |  |  |  |  | RC0603FR-071KL
 |  | R112 | R | Device:R | Resistor_SMD:R_0603_1608Metric | ~ |  |  |  |  | RC0603FR-071KL
 |  | R114 | R | Device:R | Resistor_SMD:R_0603_1608Metric | ~ |  |  |  |  | RC0603FR-071KL
 |  | R115 | R | Device:R | Resistor_SMD:R_0603_1608Metric | ~ |  |  |  |  | RC0603FR-071KL
 |  | R116 | R | Device:R | Resistor_SMD:R_0603_1608Metric | ~ |  |  |  |  | RC0603FR-071KL
 |  | R117 | R | Device:R | Resistor_SMD:R_0603_1608Metric | ~ |  |  |  |  | RC0603FR-071KL
 |  | R118 | R | Device:R | Resistor_SMD:R_0603_1608Metric | ~ |  |  |  |  | RC0603FR-071KL
 |  | R120 | R | Device:R | Resistor_SMD:R_0603_1608Metric | ~ |  |  |  |  | RC0603FR-071KL
 |  | R121 | R | Device:R | Resistor_SMD:R_0603_1608Metric | ~ |  |  |  |  | RC0603FR-071KL
 |  | R123 | R | Device:R | Resistor_SMD:R_0603_1608Metric | ~ |  |  |  |  | RC0603FR-071KL
 |  | R124 | R | Device:R | Resistor_SMD:R_0603_1608Metric | ~ |  |  |  |  | RC0603FR-071KL
 |  | R125 | R | Device:R | Resistor_SMD:R_0603_1608Metric | ~ |  |  |  |  | RC0603FR-071KL
 |  | R126 | R | Device:R | Resistor_SMD:R_0603_1608Metric | ~ |  |  |  |  | RC0603FR-071KL
 |  | R127 | R | Device:R | Resistor_SMD:R_0603_1608Metric | ~ |  |  |  |  | RC0603FR-071KL
 |  | R129 | R | Device:R | Resistor_SMD:R_0603_1608Metric | ~ |  |  |  |  | RC0603FR-071KL
 |  | R130 | R | Device:R | Resistor_SMD:R_0603_1608Metric | ~ |  |  |  |  | RC0603FR-071KL
 |  | R131 | R | Device:R | Resistor_SMD:R_0603_1608Metric | ~ |  |  |  |  | RC0603FR-071KL
 |  | R132 | R | Device:R | Resistor_SMD:R_0603_1608Metric | ~ |  |  |  |  | RC0603FR-071KL
 |  | R133 | R | Device:R | Resistor_SMD:R_0603_1608Metric | ~ |  |  |  |  | RC0603FR-071KL
 |  | R135 | R | Device:R | Resistor_SMD:R_0603_1608Metric | ~ |  |  |  |  | RC0603FR-071KL
 |  | R136 | R | Device:R | Resistor_SMD:R_0603_1608Metric | ~ |  |  |  |  | RC0603FR-071KL
 |  | R137 | R | Device:R | Resistor_SMD:R_0603_1608Metric | ~ |  |  |  |  | RC0603FR-071KL
 |  | R138 | R | Device:R | Resistor_SMD:R_0603_1608Metric | ~ |  |  |  |  | RC0603FR-071KL
 |  | R139 | R | Device:R | Resistor_SMD:R_0603_1608Metric | ~ |  |  |  |  | RC0603FR-071KL
 |  | R141 | R | Device:R | Resistor_SMD:R_0603_1608Metric | ~ |  |  |  |  | RC0603FR-071KL
 |  | R142 | R | Device:R | Resistor_SMD:R_0603_1608Metric | ~ |  |  |  |  | RC0603FR-071KL
 |  | R143 | R | Device:R | Resistor_SMD:R_0603_1608Metric | ~ |  |  |  |  | RC0603FR-071KL
 |  | R144 | R | Device:R | Resistor_SMD:R_0603_1608Metric | ~ |  |  |  |  | RC0603FR-071KL
 |  | R145 | R | Device:R | Resistor_SMD:R_0603_1608Metric | ~ |  |  |  |  | RC0603FR-071KL
 |  | R146 | R | Device:R | Resistor_SMD:R_0603_1608Metric | ~ |  |  |  |  | RC0603FR-071KL
 |  | R147 | R | Device:R | Resistor_SMD:R_0603_1608Metric | ~ |  |  |  |  | RC0603FR-071KL
 |  | R148 | R | Device:R | Resistor_SMD:R_0603_1608Metric | ~ |  |  |  |  | RC0603FR-071KL
 |  | R150 | R | Device:R | Resistor_SMD:R_0603_1608Metric | ~ |  |  |  |  | RC0603FR-071KL
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

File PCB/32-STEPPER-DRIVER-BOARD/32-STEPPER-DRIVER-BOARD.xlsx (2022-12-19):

Prj: | 32-STEPPER-DRIVER-BOARD.xml |  |  |  |  | Board Qty: | 1
Co.: |  |  |  |  |  | Unit Cost: | $96.67
Prj date: | 12/19/2022 12:13:00 PM |  |  |  |  | Total Cost: | $96.67 |  |  |  |  | $97.84 | 6 of 8 parts found |  |  |  |  | $74.39 | 5 of 8 parts found |  |  |  |  | $9.61 | 2 of 8 parts found
$ date: | 2022-12-19 12:18:55
Global Part Info |  |  |  |  |  |  |  | Digi-Key |  |  |  |  |  | Mouser |  |  |  |  |  | TME
Refs | Value | Footprint | Manf | Manf# | Qty | Unit$ | Ext$ | Avail | Purch | Unit$ | MOQ | Ext$ | Cat# | Avail | Purch | Unit$ | MOQ | Ext$ | Cat# | Avail | Purch | Unit$ | MOQ | Ext$ | Cat#
D1-D4,D6-D10,D12-D16,D18-D22,D24,D25,D27-D31,D33-D37,D39-D43,D45-D52,D54-D58,D60-D64,D66-D70,D72,D73,D75-D79,D81-D85,D87-D91,D93-D100,D102-D106,D108-D112,D114-D118,D120,D121,D123-D127,D129-D133,D135-D139,D141-D148,D150-D154,D156-D160,D162-D166,D168-D172,D174-D178,D180-D184,D186-D190,D192 | LED | LED_0603_1608Metric |  | B1931NB--20C007614U1930 | 160 | $0.465 | $74.40 | 15663 | 160 | $0.465 | 1 | $74.40 | P5555-ND (https://www.digikey.com/product-detail/en/panasonic-electronic-components/ECA-1VHG102/P5555-ND/245154)
J1-J4 | MEC2-30-01-X-TH1-NP-WT | SAMTEC_MEC2-30-01-X-TH1-NP-WT | Samtec | MEC2-30-01-L-TH1-NP-WT (https://industrial.panasonic.com/cdbs/www-data/pdf/RDF0000/ABA0000C1215.pdf) | 4 | $0.860 | $3.44 | 15663 | 4 | $0.860 | 1 | $3.44 | P5555-ND (https://www.digikey.com/product-detail/en/panasonic-electronic-components/ECA-1VHG102/P5555-ND/245154) | 960 |  | $9.820 | 1 | $39.28 | 200-MEC23001LTH1NPWT (https://www.mouser.com/ProductDetail/Samtec/MEC2-30-01-L-TH1-NP-WT?qs=icabnvfcbsFDRO5cSw3K3g%3D%3D)
J5 | IPS1-125-01-S-D | SAMTEC_IPS1-125-01-S-D | Samtec | IPT1-125-01-S-D (https://suddendocs.samtec.com/catalog_english/ipt1.pdf) | 1 | $9.020 | $9.02 | 60 | 1 | $9.020 | 1 | $9.02 | SAM8112-ND (https://www.digikey.com/en/products/detail/samtec-inc/IPT1-125-01-S-D/1110468) | 13 |  | $12.980 | 1 | $12.98 | 200-IPT112501SD (https://www.mouser.com/ProductDetail/Samtec/IPT1-125-01-S-D?qs=fnpEE5GccuOKtNLfJtObdQ%3D%3D)
J6 | UMPT-06-01-X-RA-WT-P-X | SAMTEC_UMPT-06-01-X-RA-WT-P-X | Samtec | UMPT-06-01-L-RA-WT-P-TR (https://industrial.panasonic.com/cdbs/www-data/pdf/RDF0000/ABA0000C1215.pdf) | 1 | $0.860 | $0.86 | 15663 | 1 | $0.860 | 1 | $0.86 | P5555-ND (https://www.digikey.com/product-detail/en/panasonic-electronic-components/ECA-1VHG102/P5555-ND/245154) | 58 |  | $9.610 | 1 | $9.61 | 200-UMPT0601LRAWTPTR (https://www.mouser.com/ProductDetail/Samtec/UMPT-06-01-L-RA-WT-P-TR?qs=e8oIoAS2J1TrBAKmLEWGBQ%3D%3D)
J7-J10 | Screw_Terminal_01x01 | MountingHole_2.2mm_M2_Pad |  |  | 4
JP1,JP2 | SolderJumper_2_Open | SolderJumper-2_P1.3mm_Open_RoundedPad1.0x1.5mm |  |  | 2
R1-R4,R6-R10,R12-R16,R18-R22,R24,R25,R27-R31,R33-R37,R39-R43,R45-R52,R54-R58,R60-R64,R66-R70,R72,R73,R75-R79,R81-R85,R87-R91,R93-R100,R102-R106,R108-R112,R114-R118,R120,R121,R123-R127,R129-R133,R135-R139,R141-R148,R150-R154,R156-R160,R162-R166,R168-R172,R174-R178,R180-R184,R186-R190,R192 | R | R_0603_1608Metric |  | RC0603FR-071KL | 160 | $0.007 | $1.12 | 27703508 | 160 | $0.008 | 1 | $1.34 | 311-1.00KHRCT-ND (https://www.digikey.com/en/products/detail/yageo/RC0603FR-071KL/726843) | 12010386 |  | $0.007 | 1 | $1.12 | 603-RC0603FR-071KL (https://www.mouser.com/ProductDetail/YAGEO/RC0603FR-071KL?qs=VU8sRB4EgwApHsk4rF%2F3zg%3D%3D) | 784800 |  | $0.011 | 100 | $1.78 | SMD0603-1K-1%
U1-U7,U9-U21 | 74HC595 | TSSOP-16_4.4x5mm_P0.65mm |  | MC74HC595ADTG (http://www.ti.com/lit/ds/symlink/sn74hc595.pdf) | 20 | $0.392 | $7.83 | 904 | 20 | $0.439 | 1 | $8.78 | MC74HC595ADTGOS-ND (https://www.digikey.com/en/products/detail/on-semiconductor/MC74HC595ADTG/1480112) | 9176 |  | $0.570 | 1 | $11.40 | 863-MC74HC595ADTG (https://www.mouser.com/ProductDetail/onsemi/MC74HC595ADTG?qs=qg33o%252B8vzFqSfcAj9bXV3g%3D%3D) | 12 |  | $0.392 | 5 | $7.83 | MC74HC595ADTG
 |  |  |  |  |  | Total Purchase: | $97.84 | Buy here (https://www.digikey.com/ordering/shoppingcart) | 6 of 6 parts purchased |  |  | $97.84 |  | Buy here (https://mouser.com/bom/) |  |  |  | $0.00 |  | Buy here (https://www.tme.eu/en/Profile/QuickBuy/load.html) |  |  |  | $0.00
KiCost® v1.1.12 |  |  |  |  |  | Purchase description: |  |  | 160,P5555-ND,D1-D4;D6-D10;D12-D16;D18-D22;D24;D25;D27-D31;D33-D37;D39-D43;D45-D52;D54-D58;D60-D64;D66-D70;D72;D73;D75-D79;D81-D85;D87-D91;D93-D100;D102-D106;D108-D112;D114-D118;D120;D121;D123-D127;D129-D133;D135-D139;D141-D148;D150-D154;D156-D160;D162-D166;D168-D172;D174-D178;D180-D184;D186-D190;D192 4,P5555-ND,J1-J4 1,SAM8112-ND,J5 1,P5555-ND,J6 160,311-1.00KHRCT-ND,R1-R4;R6-R10;R12-R16;R18-R22;R24;R25;R27-R31;R33-R37;R39-R43;R45-R52;R54-R58;R60-R64;R66-R70;R72;R73;R75-R79;R81-R85;R87-R91;R93-R100;R102-R106;R108-R112;R114-R118;R120;R121;R123-R127;R129-R133;R135-R139;R141-R148;R150-R154;R156-R160;R162-R166;R168-R172;R174-R178;R180-R184;R186-R190;R192 20,MC74HC595ADTGOS-ND,U1-U7;U9-U21

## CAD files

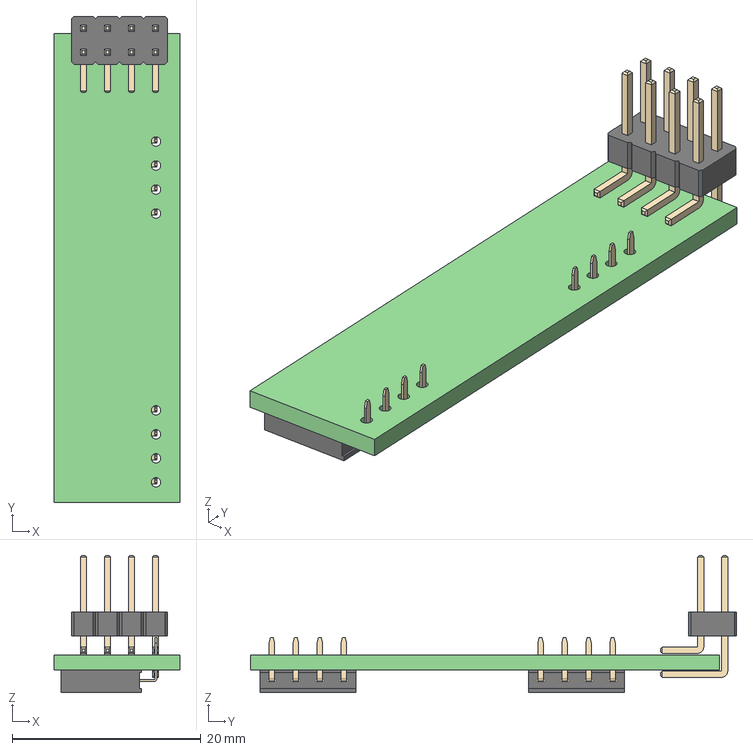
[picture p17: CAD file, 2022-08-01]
PCB/2-STEPPER-BREAKOUT/2-STEPPER-BREAKOUT_MIR.step
13.3 x 51.5 x 14.5 mm
2-STEPPER-BREAKOUT PCB

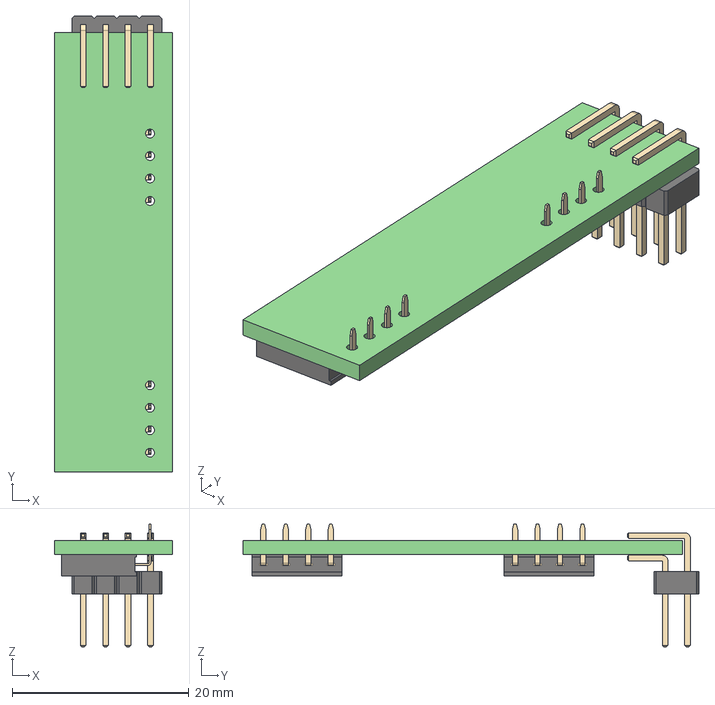
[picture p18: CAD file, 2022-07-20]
PCB/2-STEPPER-BREAKOUT/2-STEPPER-BREAKOUT.step
13.3 x 51.5 x 13.9 mm
2-STEPPER-BREAKOUT PCB

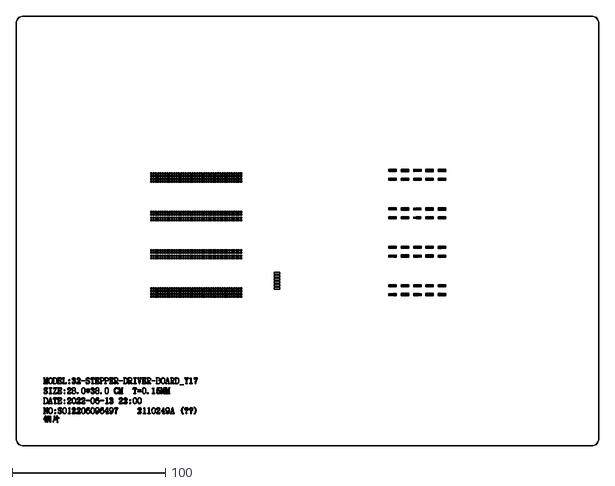
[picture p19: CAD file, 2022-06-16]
DOCUMENTS/STENCILS/32-STEPPER-DRIVER-BOARD-REV-A-STENCIL/SO12206096497.DXF
380.0 x 280.0

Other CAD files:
DOCUMENTS/REFERENCE DESIGN/Auidio_Conversion_Flow.dwg
DOCUMENTS/REFERENCE DESIGN/Physical layout conceptual.dwg
DOCUMENTS/REFERENCE DESIGN/64_MOTOR_CONCEPTUAL.dwg

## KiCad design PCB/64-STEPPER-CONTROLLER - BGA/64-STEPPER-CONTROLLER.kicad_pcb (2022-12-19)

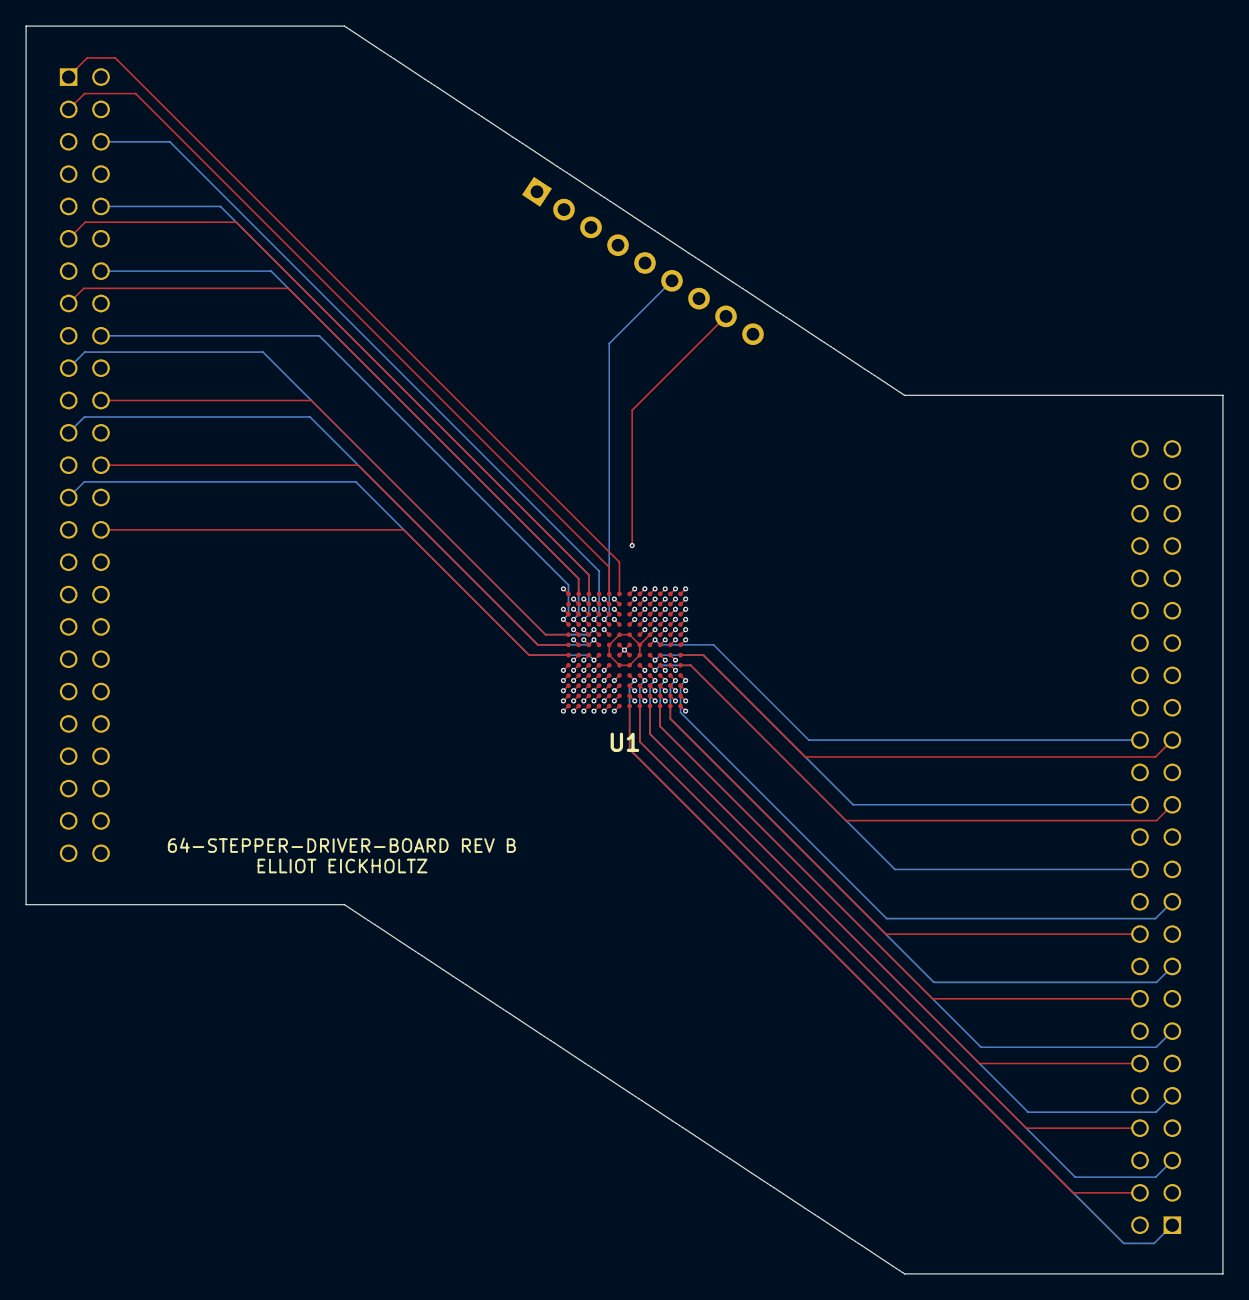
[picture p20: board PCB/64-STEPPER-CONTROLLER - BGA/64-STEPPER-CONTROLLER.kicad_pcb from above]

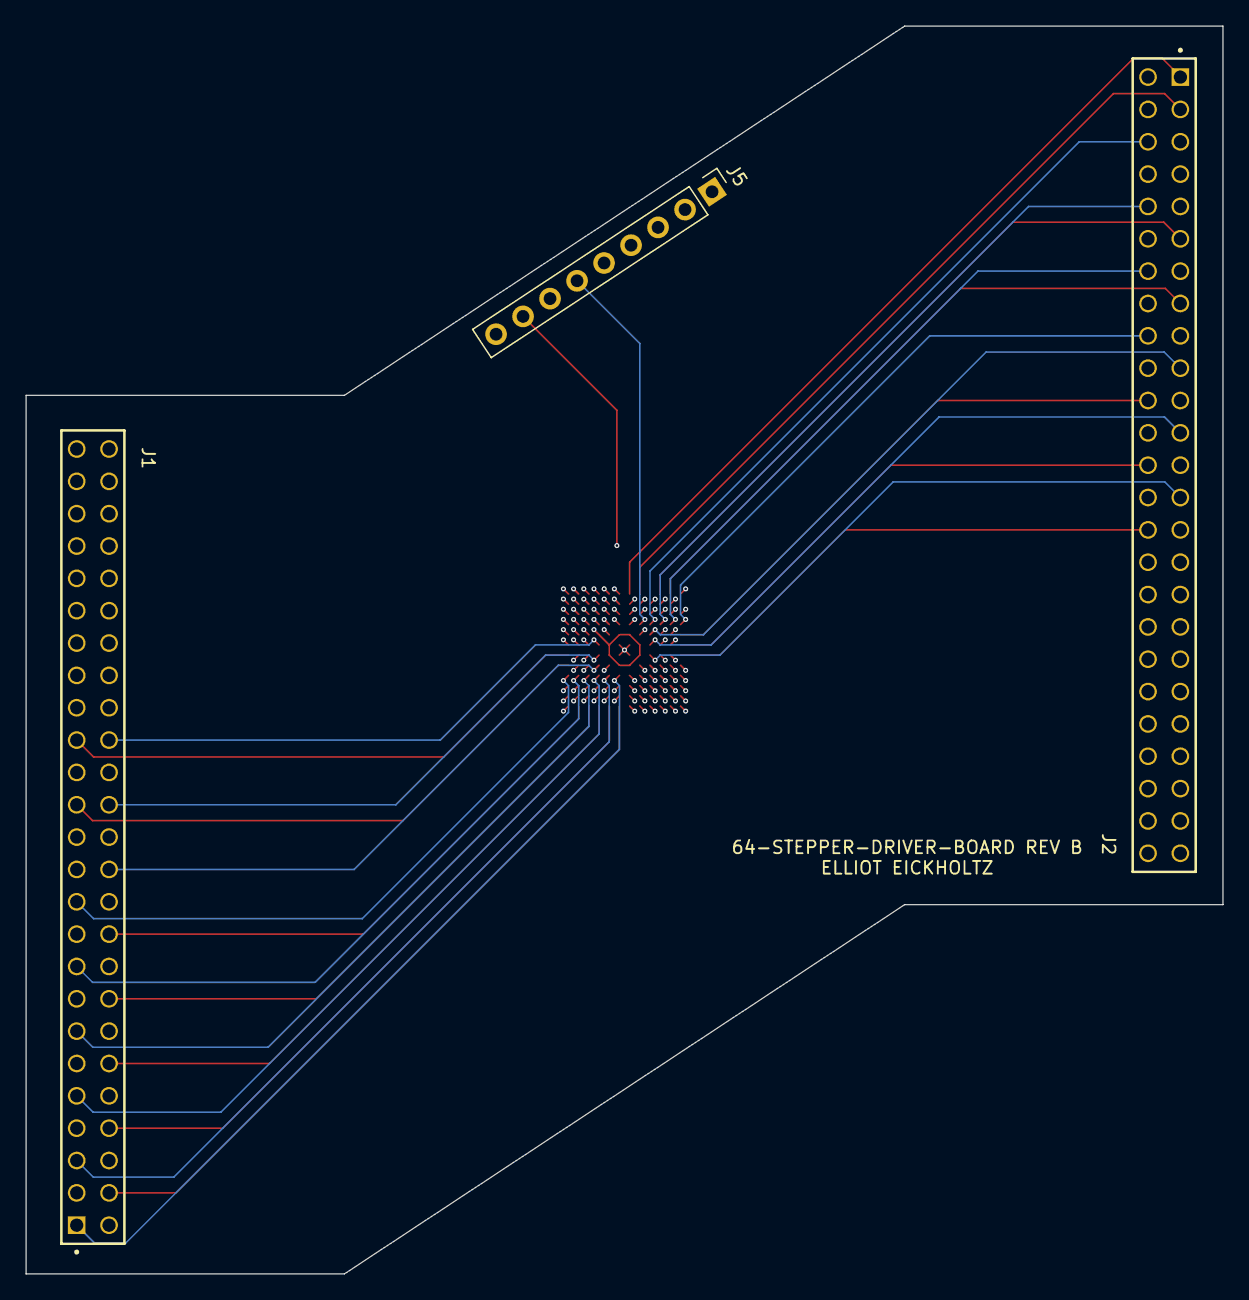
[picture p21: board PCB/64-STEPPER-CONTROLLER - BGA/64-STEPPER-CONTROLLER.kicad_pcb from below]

Board: 6 copper layers, 94.0 x 98.0 mm, 4 parts (3 on the bottom side), 69 nets.

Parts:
J1, J2: IPS1-125-01-S-D; SAMTEC_IPS1-125-01-S-D
J5: Conn_01x09; PinHeader_1x09_P2.54mm_Vertical
U1: STM32L471ZGJ6; BGA144C80P12X12_1000X1000X60

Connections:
1A1STEP: J1.08, U1.M8 (PE7)
1A2STEP: J1.06, U1.K8 (PE11)
1A3STEP: J1.04, U1.M7 (PF14)
1A4STEP: J1.02, U1.K7 (PG0)
1A5STEP: J1.07, U1.L8 (PE12)
1A6STEP: J1.05, U1.J8 (PE9)
1A7STEP: J1.03, U1.L7 (PE8)
1A8STEP: J1.01, U1.J7 (PG1)
2A1STEP: J1.16, U1.M10 (PE10)
2A2STEP: J1.14, U1.K10 (PB12)
2A3STEP: J1.12, U1.M9 (PF15)
2A4STEP: J1.10, U1.K9 (PB11)
2A5STEP: J1.15, U1.L10 (PE14)
2A6STEP: J1.13, U1.J10 (PB14)
2A7STEP: J1.11, U1.L9 (PE13)
2A8STEP: J1.09, U1.J9 (PB13)
3A1STEP: J1.24, U1.H9 (PD12)
3A2STEP: J1.22, U1.K12 (PD9)
3A3STEP: J1.20, U1.M11 (PE15)
3A4STEP: J1.18, U1.K11 (PD8)
3A5STEP: J1.23, U1.L12 (PB15)
3A6STEP: J1.21, U1.J12 (PD15)
3A7STEP: J1.19, U1.L11 (PB10)
3A8STEP: J1.17, U1.J11 (PD10)
4A1STEP: J1.32, U1.F9 (PG7)
4A2STEP: J1.30, U1.G11 (PG3)
4A3STEP: J1.28, U1.G9 (PG4)
4A4STEP: J1.26, U1.H11 (PD14)
4A5STEP: J1.31, U1.G12 (PG5)
4A6STEP: J1.29, U1.G10 (PD13)
4A7STEP: J1.27, U1.H12 (PG2)
4A8STEP: J1.25, U1.H10 (PD11)
5A1STEP: J2.08, U1.B5 (PB6)
5A2STEP: J2.06, U1.D4 (PC13)
5A3STEP: J2.04, U1.B6 (PG15)
5A4STEP: J2.02, U1.D6 (PG13)
5A5STEP: J2.07, U1.B4 (PE1)
5A6STEP: J2.05, U1.C4 (PB9)
5A7STEP: J2.03, U1.A5 (PB7)
5A8STEP: J2.01, U1.A6 (PG14)
6A1STEP: J2.16, U1.B2 (PE4)
6A2STEP: J2.14, U1.D2 (PC14-_OSC32_IN)
6A3STEP: J2.12, U1.B3 (PE3)
6A4STEP: J2.10, U1.D3 (PE6)
6A5STEP: J2.15, U1.A2 (PE0)
6A6STEP: J2.13, U1.C2 (PE5)
6A7STEP: J2.11, U1.A3 (PB8)
6A8STEP: J2.09, U1.C3 (PE2)
7A1STEP: J2.24, U1.F3 (PF5)
7A2STEP: J2.22, U1.E1 (PF6)
7A3STEP: J2.20, U1.E3 (PF0)
7A4STEP: J2.18, U1.D1 (PF4)
7A5STEP: J2.23, U1.F4 (PF3)
7A6STEP: J2.21, U1.E2 (PF1)
7A7STEP: J2.19, U1.E4 (PF2)
7A8STEP: J2.17, U1.C1 (PC15-_OSC32_OUT)
8A1STEP: J2.32, U1.H2 (PC0)
8A2STEP: J2.30, U1.G1 (PH1-_OSC_OUT)
8A3STEP: J2.28, U1.G3 (PF10)
8A4STEP: J2.26, U1.F1 (PF8)
8A5STEP: J2.31, U1.H3 (PC1)
8A6STEP: J2.29, U1.G2 (PH0-OSC_IN)
8A7STEP: J2.27, U1.G4 (PF9)
8A8STEP: J2.25, U1.F2 (PF7)
+5V: J5.9, U1.E6 (VDDIO2), U1.E7 (VDD), U1.E9 (VDD), U1.F5 (VDD), U1.F8 (VDDIO2), U1.G5 (VDD), U1.G8 (VDD), U1.H6 (VDD), U1.H7 (VDD), U1.K2 (VDDA)
GND: J1.47, J1.48, J1.49, J1.50, J2.47, J2.48, J2.49, J2.50, J5.5, U1.A1 (VSS), U1.E5 (VSS), U1.E8 (VSS), U1.F6 (VSS), U1.F7 (VSS), U1.G6 (VSS), U1.G7 (VSS), U1.H5 (VSS), U1.H8 (VSS), U1.J1 (VSSA), U1.M1 (VSS), U1.M12 (VSS)
MISO: J5.6, U1.D5 (PB4)
MOSI: J5.8, U1.C5 (PB5)
SCK: J5.7, U1.C6 (PB3)

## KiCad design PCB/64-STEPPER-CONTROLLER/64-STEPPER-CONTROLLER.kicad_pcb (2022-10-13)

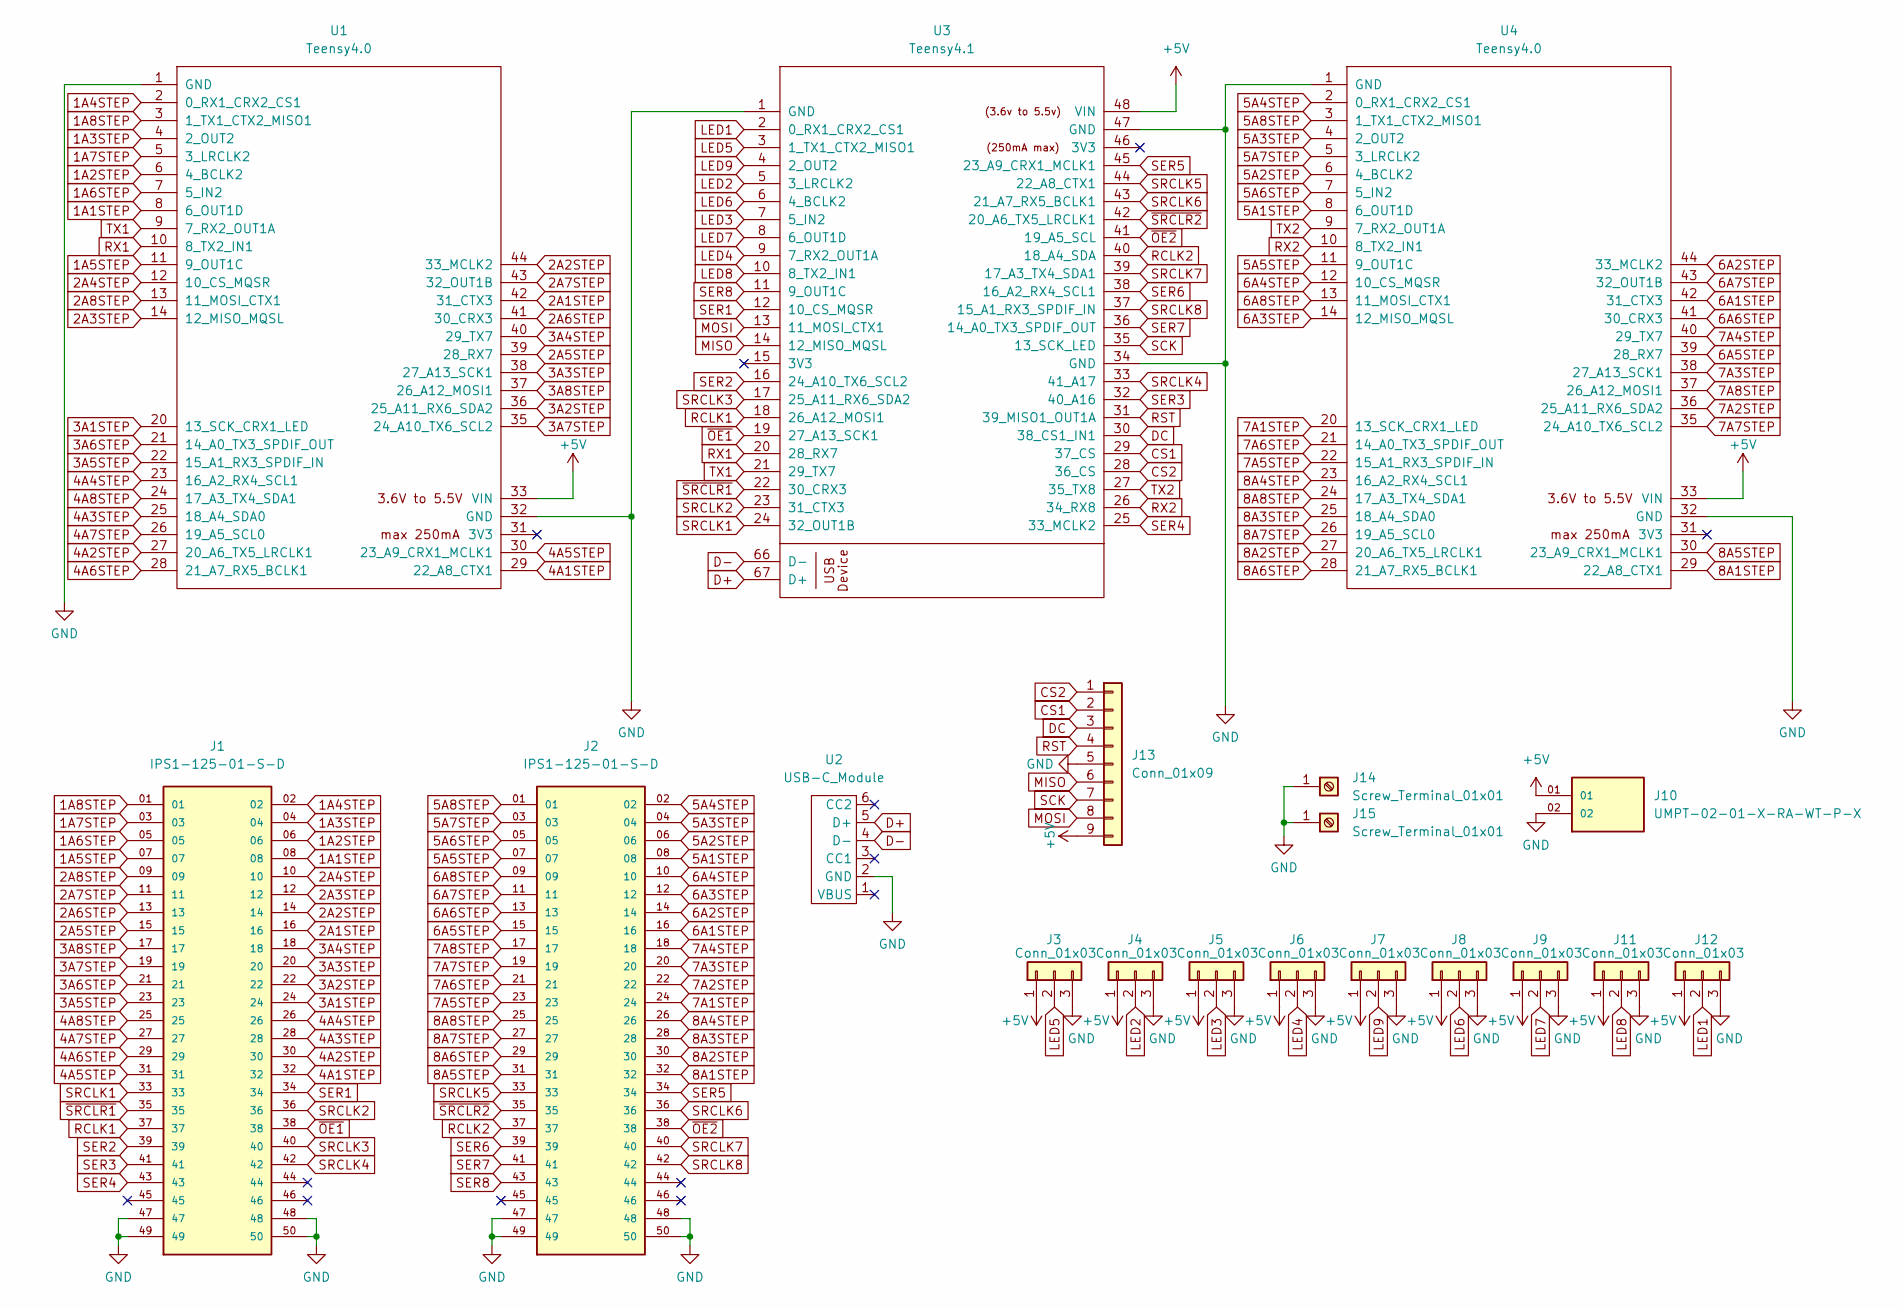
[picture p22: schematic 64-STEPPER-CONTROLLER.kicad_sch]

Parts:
J1, J2: IPS1-125-01-S-D; SAMTEC_IPS1-125-01-S-D; PARTREV R
J3, J4, J5, J6, J7, J8, J9, J11, J12: Conn_01x03; 3-PIN TERMINAL
J10: UMPT-02-01-X-RA-WT-P-X; SAMTEC_UMPT-02-01-X-RA-WT-P-X; PARTREV 4
J13: Conn_01x09; PinHeader_1x09_P2.54mm_Vertical
J14, J15: Screw_Terminal_01x01; MountingHole_2.2mm_M2_Pad
U1, U4: Teensy4.0; Teensy40
U2: USB-C_Module; USB-C-MODULE
U3: Teensy4.1; Teensy41

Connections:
1A1STEP: J1.08, U1.8 (6_OUT1D)
1A2STEP: J1.06, U1.6 (4_BCLK2)
1A3STEP: J1.04, U1.4 (2_OUT2)
1A4STEP: J1.02, U1.2 (0_RX1_CRX2_CS1)
1A5STEP: J1.07, U1.11 (9_OUT1C)
1A6STEP: J1.05, U1.7 (5_IN2)
1A7STEP: J1.03, U1.5 (3_LRCLK2)
1A8STEP: J1.01, U1.3 (1_TX1_CTX2_MISO1)
2A1STEP: J1.16, U1.42 (31_CTX3)
2A2STEP: J1.14, U1.44 (33_MCLK2)
2A3STEP: J1.12, U1.14 (12_MISO_MQSL)
2A4STEP: J1.10, U1.12 (10_CS_MQSR)
2A5STEP: J1.15, U1.39 (28_RX7)
2A6STEP: J1.13, U1.41 (30_CRX3)
2A7STEP: J1.11, U1.43 (32_OUT1B)
2A8STEP: J1.09, U1.13 (11_MOSI_CTX1)
3A1STEP: J1.24, U1.20 (13_SCK_CRX1_LED)
3A2STEP: J1.22, U1.36 (25_A11_RX6_SDA2)
3A3STEP: J1.20, U1.38 (27_A13_SCK1)
3A4STEP: J1.18, U1.40 (29_TX7)
3A5STEP: J1.23, U1.22 (15_A1_RX3_SPDIF_IN)
3A6STEP: J1.21, U1.21 (14_A0_TX3_SPDIF_OUT)
3A7STEP: J1.19, U1.35 (24_A10_TX6_SCL2)
3A8STEP: J1.17, U1.37 (26_A12_MOSI1)
4A1STEP: J1.32, U1.29 (22_A8_CTX1)
4A2STEP: J1.30, U1.27 (20_A6_TX5_LRCLK1)
4A3STEP: J1.28, U1.25 (18_A4_SDA0)
4A4STEP: J1.26, U1.23 (16_A2_RX4_SCL1)
4A5STEP: J1.31, U1.30 (23_A9_CRX1_MCLK1)
4A6STEP: J1.29, U1.28 (21_A7_RX5_BCLK1)
4A7STEP: J1.27, U1.26 (19_A5_SCL0)
4A8STEP: J1.25, U1.24 (17_A3_TX4_SDA1)
5A1STEP: J2.08, U4.8 (6_OUT1D)
5A2STEP: J2.06, U4.6 (4_BCLK2)
5A3STEP: J2.04, U4.4 (2_OUT2)
5A4STEP: J2.02, U4.2 (0_RX1_CRX2_CS1)
5A5STEP: J2.07, U4.11 (9_OUT1C)
5A6STEP: J2.05, U4.7 (5_IN2)
5A7STEP: J2.03, U4.5 (3_LRCLK2)
5A8STEP: J2.01, U4.3 (1_TX1_CTX2_MISO1)
6A1STEP: J2.16, U4.42 (31_CTX3)
6A2STEP: J2.14, U4.44 (33_MCLK2)
6A3STEP: J2.12, U4.14 (12_MISO_MQSL)
6A4STEP: J2.10, U4.12 (10_CS_MQSR)
6A5STEP: J2.15, U4.39 (28_RX7)
6A6STEP: J2.13, U4.41 (30_CRX3)
6A7STEP: J2.11, U4.43 (32_OUT1B)
6A8STEP: J2.09, U4.13 (11_MOSI_CTX1)
7A1STEP: J2.24, U4.20 (13_SCK_CRX1_LED)
7A2STEP: J2.22, U4.36 (25_A11_RX6_SDA2)
7A3STEP: J2.20, U4.38 (27_A13_SCK1)
7A4STEP: J2.18, U4.40 (29_TX7)
7A5STEP: J2.23, U4.22 (15_A1_RX3_SPDIF_IN)
7A6STEP: J2.21, U4.21 (14_A0_TX3_SPDIF_OUT)
7A7STEP: J2.19, U4.35 (24_A10_TX6_SCL2)
7A8STEP: J2.17, U4.37 (26_A12_MOSI1)
8A1STEP: J2.32, U4.29 (22_A8_CTX1)
8A2STEP: J2.30, U4.27 (20_A6_TX5_LRCLK1)
8A3STEP: J2.28, U4.25 (18_A4_SDA0)
8A4STEP: J2.26, U4.23 (16_A2_RX4_SCL1)
8A5STEP: J2.31, U4.30 (23_A9_CRX1_MCLK1)
8A6STEP: J2.29, U4.28 (21_A7_RX5_BCLK1)
8A7STEP: J2.27, U4.26 (19_A5_SCL0)
8A8STEP: J2.25, U4.24 (17_A3_TX4_SDA1)
+5V: J3.1, J4.1, J5.1, J6.1, J7.1, J8.1, J9.1, J10.01, J11.1, J12.1, J13.9, U1.33 (VIN), U3.48 (VIN), U4.33 (VIN)
CS1: J13.2, U3.29 (37_CS)
CS2: J13.1, U3.28 (36_CS)
D+: U2.5 (D+), U3.67 (D+)
D-: U2.4 (D-), U3.66 (D-)
DC: J13.3, U3.30 (38_CS1_IN1)
GND: J1.47, J1.48, J1.49, J1.50, J2.47, J2.48, J2.49, J2.50, J3.3, J4.3, J5.3, J6.3, J7.3, J8.3, J9.3, J10.02, J11.3, J12.3, J13.5, J14.1, J15.1, U1.1 (GND), U1.32 (GND), U2.2 (GND), U3.1 (GND), U3.34 (GND), U3.47 (GND), U4.1 (GND), U4.32 (GND)
LED1: J12.2, U3.2 (0_RX1_CRX2_CS1)
LED2: J4.2, U3.5 (3_LRCLK2)
LED3: J5.2, U3.7 (5_IN2)
LED4: J6.2, U3.9 (7_RX2_OUT1A)
LED5: J3.2, U3.3 (1_TX1_CTX2_MISO1)
LED6: J8.2, U3.6 (4_BCLK2)
LED7: J9.2, U3.8 (6_OUT1D)
LED8: J11.2, U3.10 (8_TX2_IN1)
LED9: J7.2, U3.4 (2_OUT2)
MISO: J13.6, U3.14 (12_MISO_MQSL)
MOSI: J13.8, U3.13 (11_MOSI_CTX1)
RCLK1: J1.37, U3.18 (26_A12_MOSI1)
RCLK2: J2.37, U3.40 (18_A4_SDA)
RST: J13.4, U3.31 (39_MISO1_OUT1A)
RX1: U1.10 (8_TX2_IN1), U3.20 (28_RX7)
RX2: U3.26 (34_RX8), U4.10 (8_TX2_IN1)
SCK: J13.7, U3.35 (13_SCK_LED)
SER1: J1.34, U3.12 (10_CS_MQSR)
SER2: J1.39, U3.16 (24_A10_TX6_SCL2)
SER3: J1.41, U3.32 (40_A16)
SER4: J1.43, U3.25 (33_MCLK2)
SER5: J2.34, U3.45 (23_A9_CRX1_MCLK1)
SER6: J2.39, U3.38 (16_A2_RX4_SCL1)
SER7: J2.41, U3.36 (14_A0_TX3_SPDIF_OUT)
SER8: J2.43, U3.11 (9_OUT1C)
SRCLK1: J1.33, U3.24 (32_OUT1B)
SRCLK2: J1.36, U3.23 (31_CTX3)
SRCLK3: J1.40, U3.17 (25_A11_RX6_SDA2)
SRCLK4: J1.42, U3.33 (41_A17)
SRCLK5: J2.33, U3.44 (22_A8_CTX1)
SRCLK6: J2.36, U3.43 (21_A7_RX5_BCLK1)
SRCLK7: J2.40, U3.39 (17_A3_TX4_SDA1)
SRCLK8: J2.42, U3.37 (15_A1_RX3_SPDIF_IN)
TX1: U1.9 (7_RX2_OUT1A), U3.21 (29_TX7)
TX2: U3.27 (35_TX8), U4.9 (7_RX2_OUT1A)
~OE1: J1.38, U3.19 (27_A13_SCK1)
~OE2: J2.38, U3.41 (19_A5_SCL)
~SRCLR1: J1.35, U3.22 (30_CRX3)
~SRCLR2: J2.35, U3.42 (20_A6_TX5_LRCLK1)

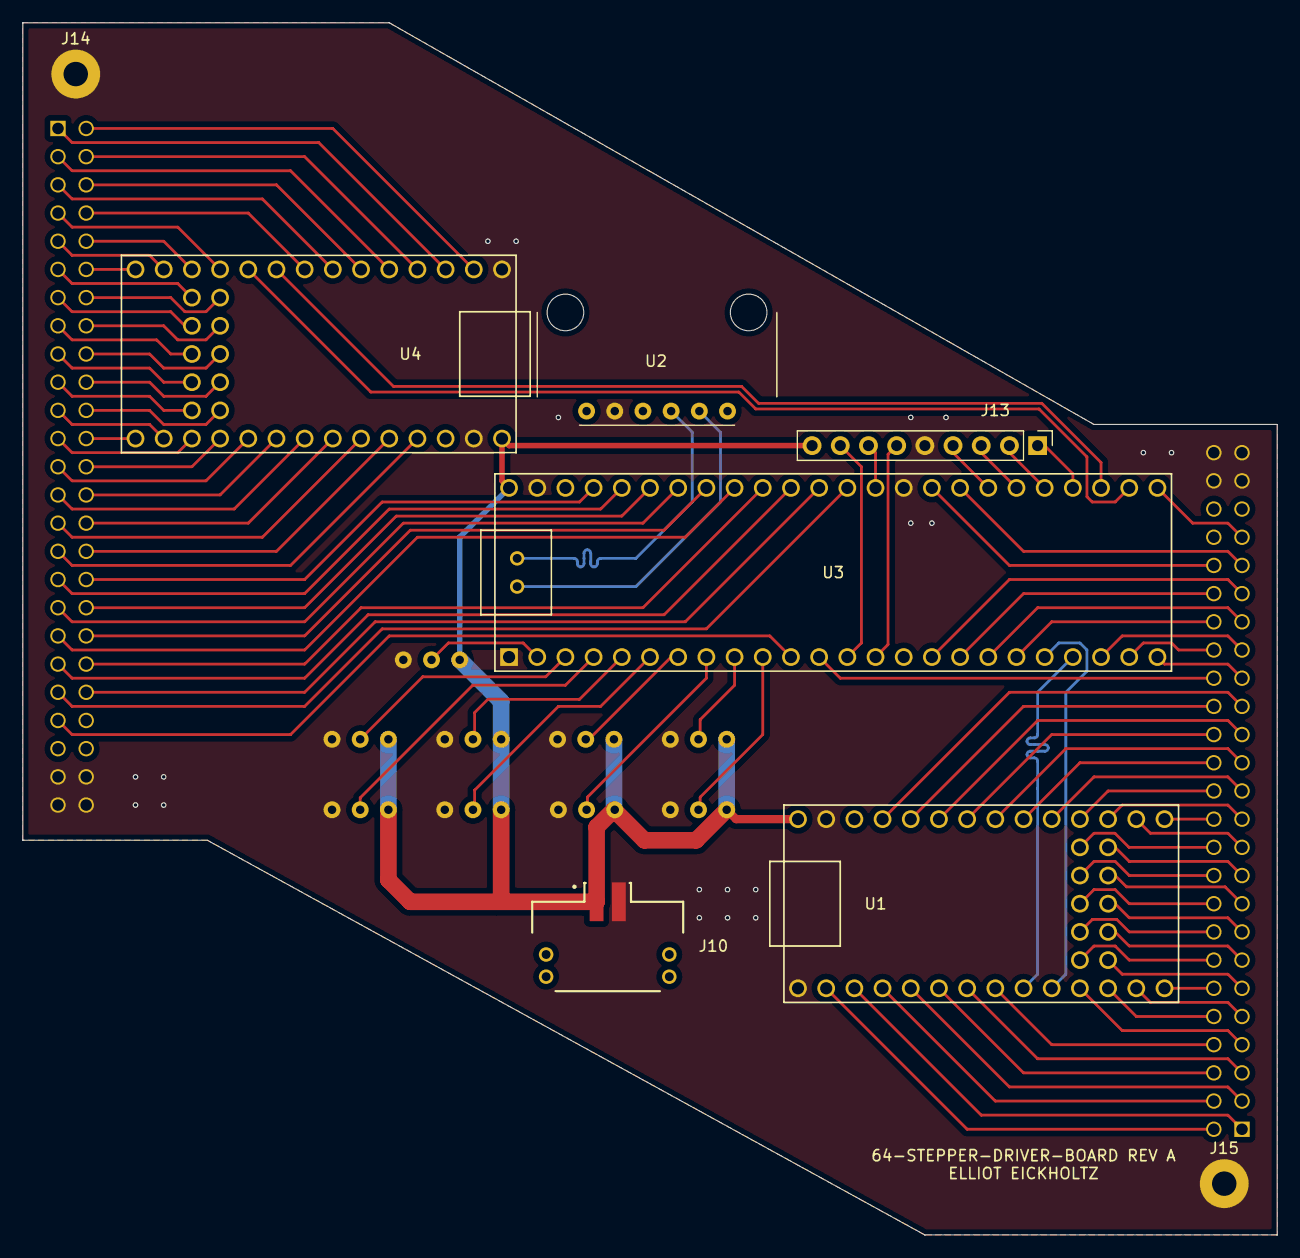
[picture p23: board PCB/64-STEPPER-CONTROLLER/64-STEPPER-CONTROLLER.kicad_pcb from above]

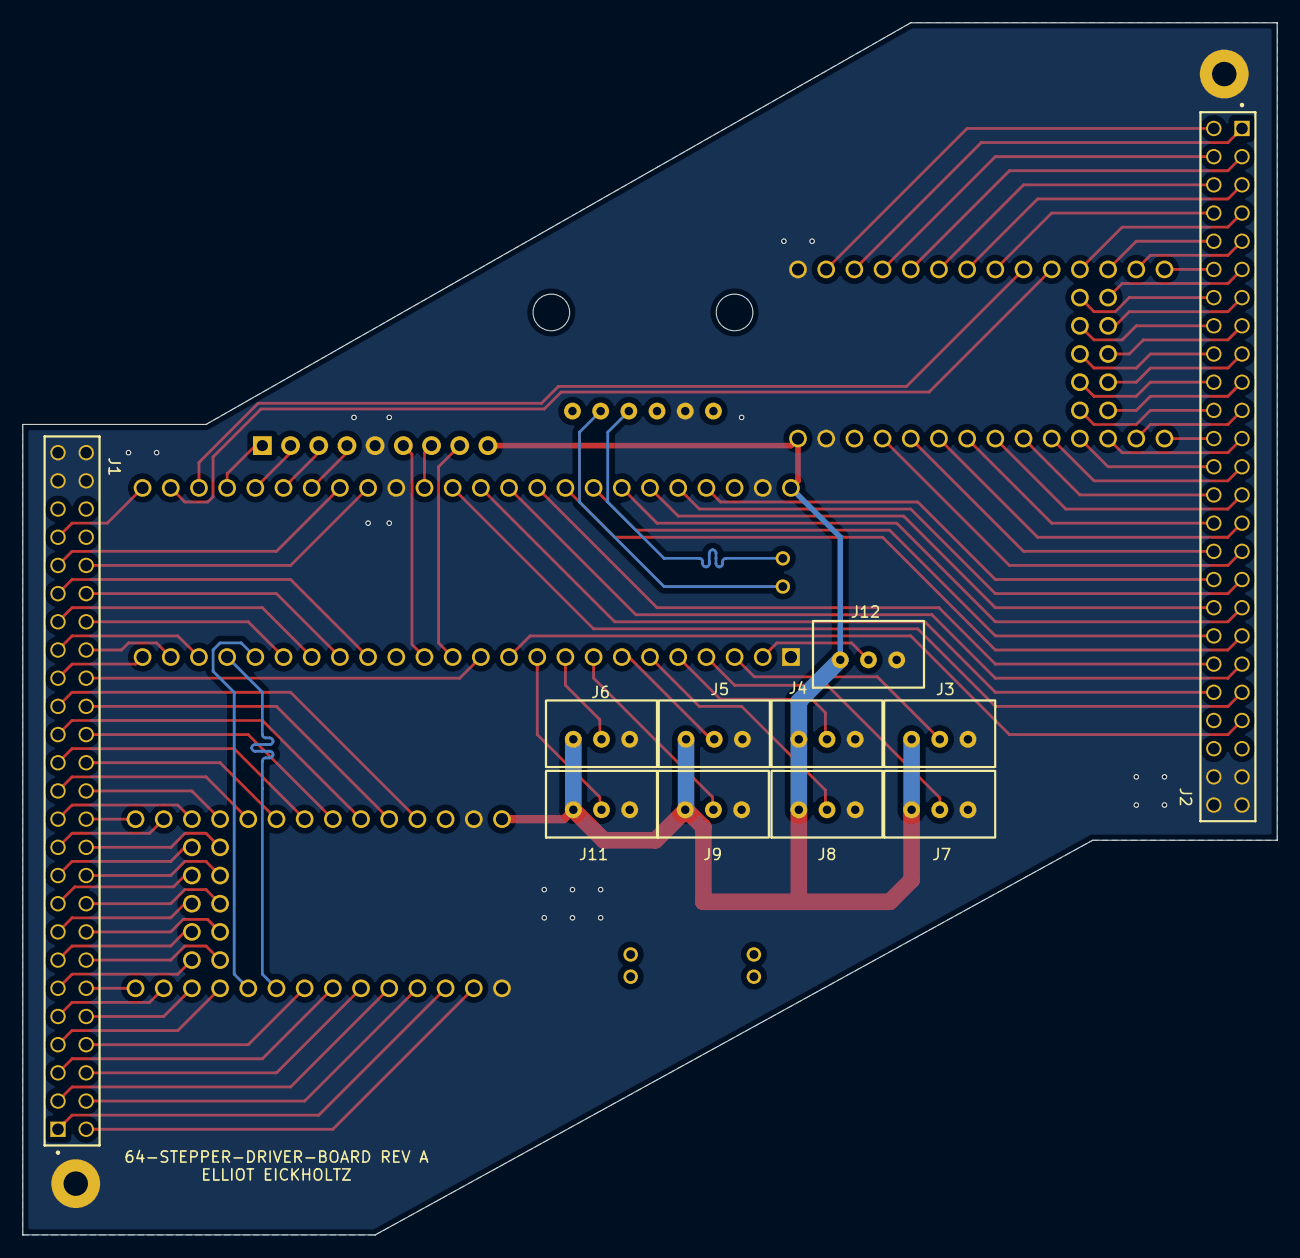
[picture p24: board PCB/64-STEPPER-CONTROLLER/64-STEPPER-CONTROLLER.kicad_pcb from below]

Board: 2 copper layers, 113.0 x 109.2 mm, 19 parts (11 on the bottom side), 110 nets.

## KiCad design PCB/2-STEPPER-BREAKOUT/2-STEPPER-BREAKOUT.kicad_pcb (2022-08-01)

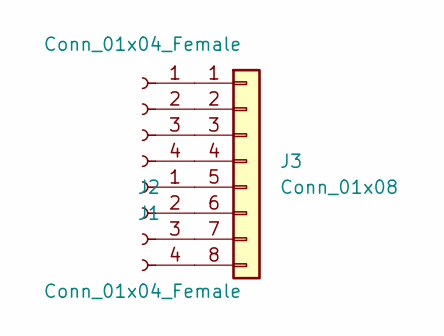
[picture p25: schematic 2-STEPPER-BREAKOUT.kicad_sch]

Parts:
J1, J2: Conn_01x04_Female; PinSocket_1x04_P2.54mm_Horizontal
J3: Conn_01x08; PinHeader_2x04_P2.54mm_edge

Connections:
unnamed: J1.1, J3.1
unnamed: J1.2, J3.2
unnamed: J1.3, J3.3
unnamed: J1.4, J3.4
unnamed: J2.1, J3.5
unnamed: J2.2, J3.6
unnamed: J2.3, J3.7
unnamed: J2.4, J3.8

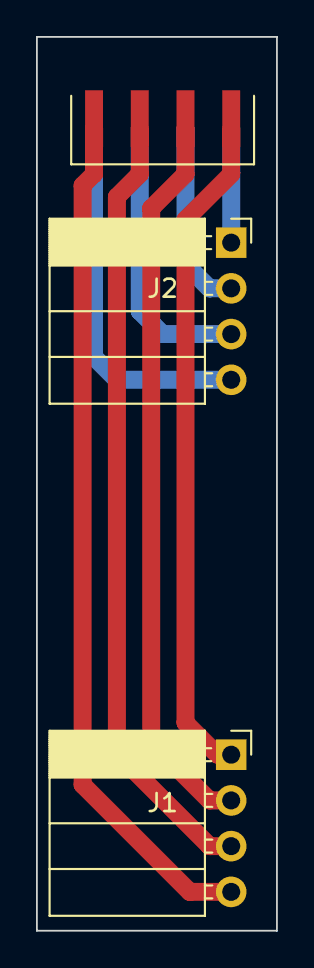
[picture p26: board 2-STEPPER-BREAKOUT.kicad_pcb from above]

Board: 2 copper layers, 13.3 x 49.7 mm, 3 parts (0 on the bottom side), 8 nets.

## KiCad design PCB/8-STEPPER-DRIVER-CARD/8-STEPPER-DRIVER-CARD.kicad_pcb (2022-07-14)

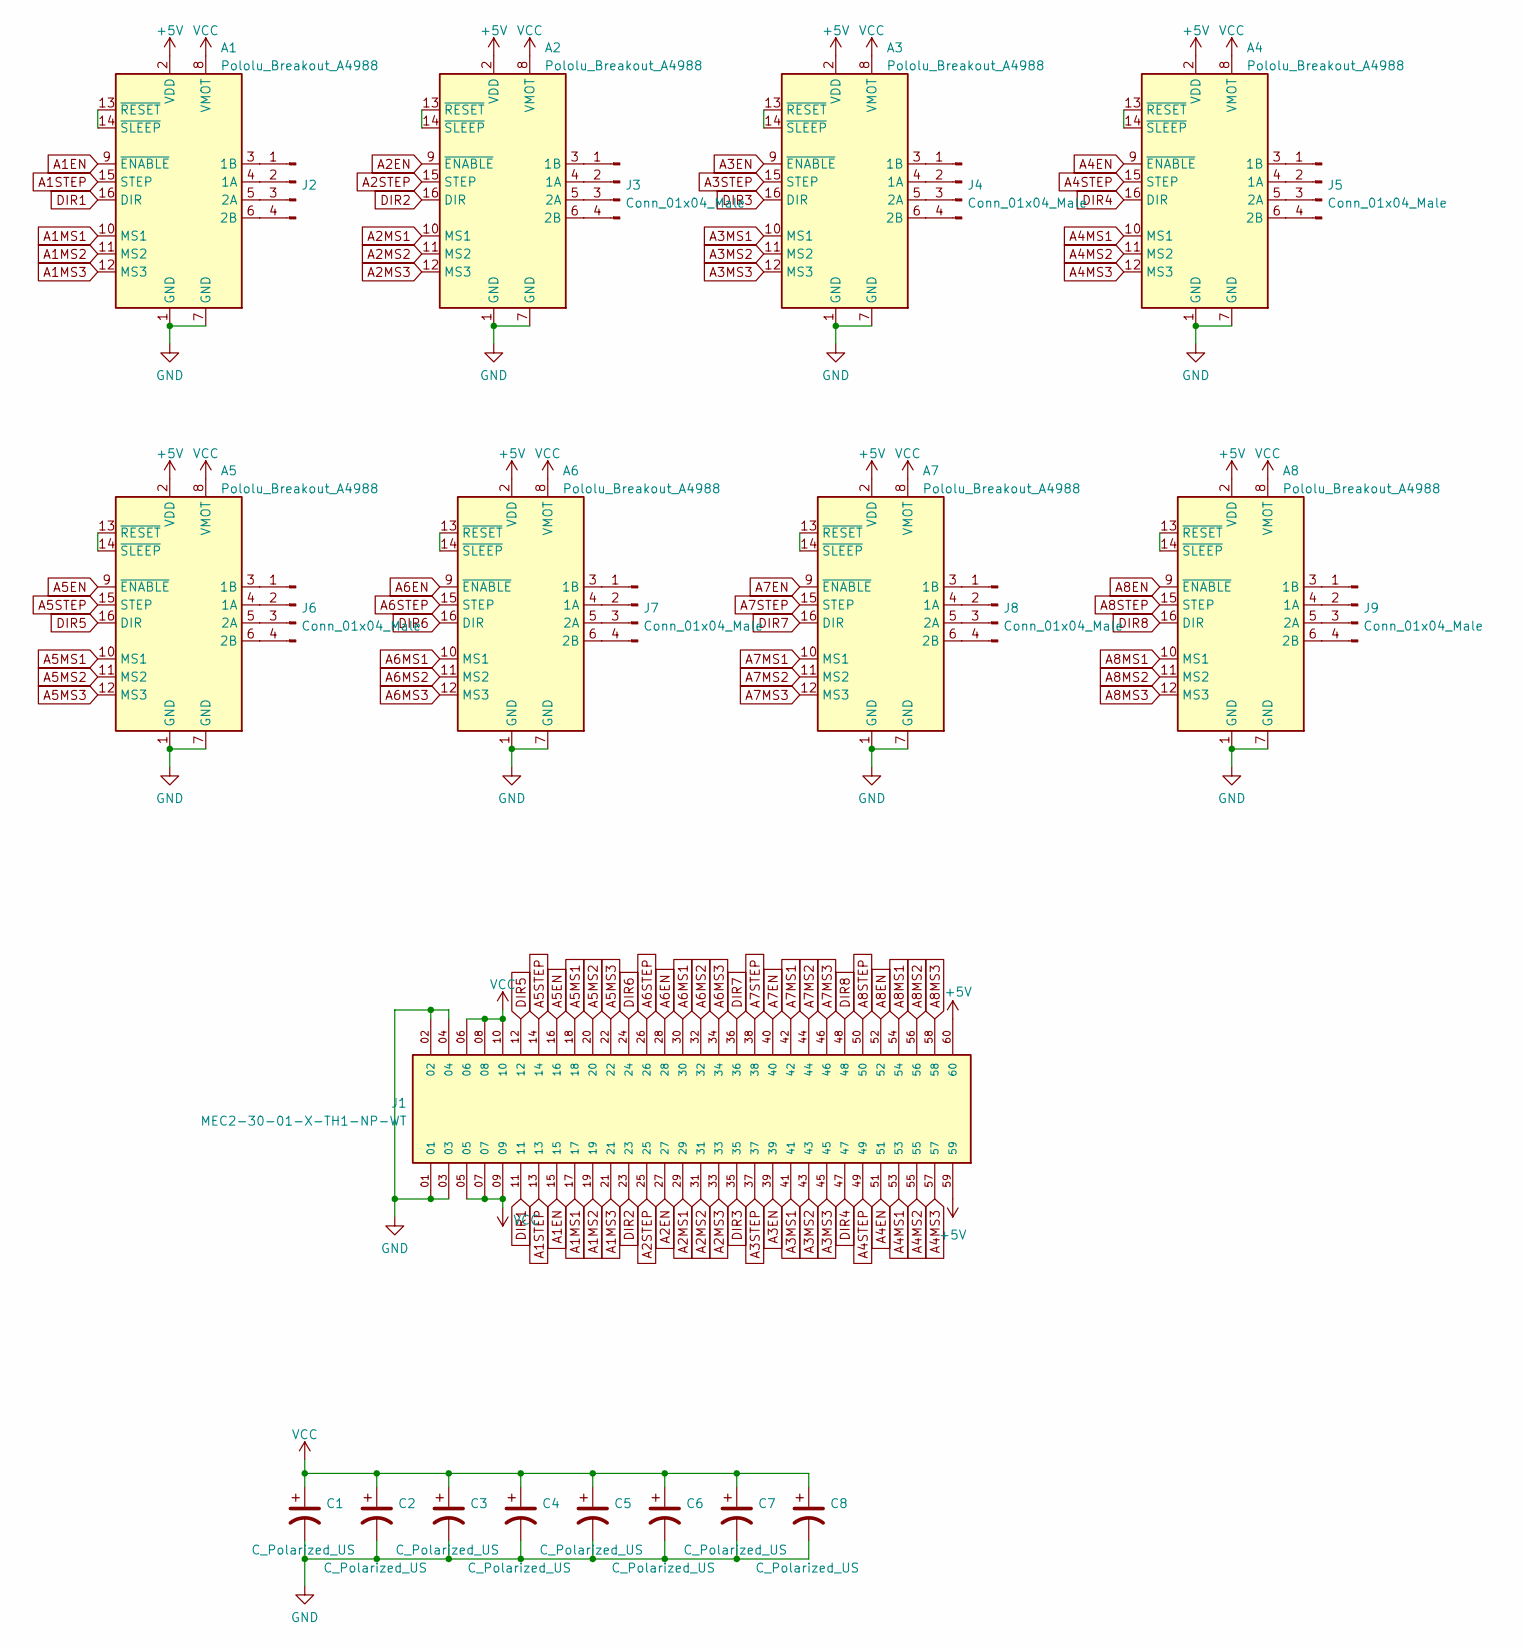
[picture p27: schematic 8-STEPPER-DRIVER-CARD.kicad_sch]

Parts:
A1, A2, A3, A4, A5, A6, A7, A8: Pololu_Breakout_A4988; Pololu_Breakout-16_15.2x20.3mm
C1, C2, C3, C4, C5, C6, C7, C8: C_Polarized_US; CP_Radial_D6.3mm_P2.50mm
J1: MEC2-30-01-X-TH1-NP-WT; MEC2-30-01-J-TH1-NP-WT-EDGECARD; PARTREV F
J2: (no value)
J3, J4, J5, J6, J7, J8, J9: Conn_01x04_Male

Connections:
+5V: A1.2 (VDD), A2.2 (VDD), A3.2 (VDD), A4.2 (VDD), A5.2 (VDD), A6.2 (VDD), A7.2 (VDD), A8.2 (VDD), J1.59, J1.60
A1EN: A1.9 (~ENABLE), J1.15
A1MS1: A1.10 (MS1), J1.17
A1MS2: A1.11 (MS2), J1.19
A1MS3: A1.12 (MS3), J1.21
A1STEP: A1.15 (STEP), J1.13
A2EN: A2.9 (~ENABLE), J1.27
A2MS1: A2.10 (MS1), J1.29
A2MS2: A2.11 (MS2), J1.31
A2MS3: A2.12 (MS3), J1.33
A2STEP: A2.15 (STEP), J1.25
A3EN: A3.9 (~ENABLE), J1.39
A3MS1: A3.10 (MS1), J1.41
A3MS2: A3.11 (MS2), J1.43
A3MS3: A3.12 (MS3), J1.45
A3STEP: A3.15 (STEP), J1.37
A4EN: A4.9 (~ENABLE), J1.51
A4MS1: A4.10 (MS1), J1.53
A4MS2: A4.11 (MS2), J1.55
A4MS3: A4.12 (MS3), J1.57
A4STEP: A4.15 (STEP), J1.49
A5EN: A5.9 (~ENABLE), J1.16
A5MS1: A5.10 (MS1), J1.18
A5MS2: A5.11 (MS2), J1.20
A5MS3: A5.12 (MS3), J1.22
A5STEP: A5.15 (STEP), J1.14
A6EN: A6.9 (~ENABLE), J1.28
A6MS1: A6.10 (MS1), J1.30
A6MS2: A6.11 (MS2), J1.32
A6MS3: A6.12 (MS3), J1.34
A6STEP: A6.15 (STEP), J1.26
A7EN: A7.9 (~ENABLE), J1.40
A7MS1: A7.10 (MS1), J1.42
A7MS2: A7.11 (MS2), J1.44
A7MS3: A7.12 (MS3), J1.46
A7STEP: A7.15 (STEP), J1.38
A8EN: A8.9 (~ENABLE), J1.52
A8MS1: A8.10 (MS1), J1.54
A8MS2: A8.11 (MS2), J1.56
A8MS3: A8.12 (MS3), J1.58
A8STEP: A8.15 (STEP), J1.50
DIR1: A1.16 (DIR), J1.11
DIR2: A2.16 (DIR), J1.23
DIR3: A3.16 (DIR), J1.35
DIR4: A4.16 (DIR), J1.47
DIR5: A5.16 (DIR), J1.12
DIR6: A6.16 (DIR), J1.24
DIR7: A7.16 (DIR), J1.36
DIR8: A8.16 (DIR), J1.48
GND: A1.1 (GND), A1.7 (GND), A2.1 (GND), A2.7 (GND), A3.1 (GND), A3.7 (GND), A4.1 (GND), A4.7 (GND), A5.1 (GND), A5.7 (GND), A6.1 (GND), A6.7 (GND), A7.1 (GND), A7.7 (GND), A8.1 (GND), A8.7 (GND), C1.2, C2.2, C3.2, C4.2, C5.2, C6.2, C7.2, C8.2, J1.01, J1.02, J1.03, J1.04
unnamed: A1.3 (1B), J2.1
unnamed: A1.4 (1A), J2.2
unnamed: A1.5 (2A), J2.3
unnamed: A1.6 (2B), J2.4
unnamed: A1.13 (~RESET), A1.14 (~SLEEP)
unnamed: A2.3 (1B), J3.1
unnamed: A2.4 (1A), J3.2
unnamed: A2.5 (2A), J3.3
unnamed: A2.6 (2B), J3.4
unnamed: A2.13 (~RESET), A2.14 (~SLEEP)
unnamed: A3.3 (1B), J4.1
unnamed: A3.4 (1A), J4.2
unnamed: A3.5 (2A), J4.3
unnamed: A3.6 (2B), J4.4
unnamed: A3.13 (~RESET), A3.14 (~SLEEP)
unnamed: A4.3 (1B), J5.1
unnamed: A4.4 (1A), J5.2
unnamed: A4.5 (2A), J5.3
unnamed: A4.6 (2B), J5.4
unnamed: A4.13 (~RESET), A4.14 (~SLEEP)
unnamed: A5.3 (1B), J6.1
unnamed: A5.4 (1A), J6.2
unnamed: A5.5 (2A), J6.3
unnamed: A5.6 (2B), J6.4
unnamed: A5.13 (~RESET), A5.14 (~SLEEP)
unnamed: A6.3 (1B), J7.1
unnamed: A6.4 (1A), J7.2
unnamed: A6.5 (2A), J7.3
unnamed: A6.6 (2B), J7.4
unnamed: A6.13 (~RESET), A6.14 (~SLEEP)
unnamed: A7.3 (1B), J8.1
unnamed: A7.4 (1A), J8.2
unnamed: A7.5 (2A), J8.3
unnamed: A7.6 (2B), J8.4
unnamed: A7.13 (~RESET), A7.14 (~SLEEP)
unnamed: A8.3 (1B), J9.1
unnamed: A8.4 (1A), J9.2
unnamed: A8.5 (2A), J9.3
unnamed: A8.6 (2B), J9.4
unnamed: A8.13 (~RESET), A8.14 (~SLEEP)
VCC: A1.8 (VMOT), A2.8 (VMOT), A3.8 (VMOT), A4.8 (VMOT), A5.8 (VMOT), A6.8 (VMOT), A7.8 (VMOT), A8.8 (VMOT), C1.1, C2.1, C3.1, C4.1, C5.1, C6.1, C7.1, C8.1, J1.05, J1.06, J1.07, J1.08, J1.09, J1.10

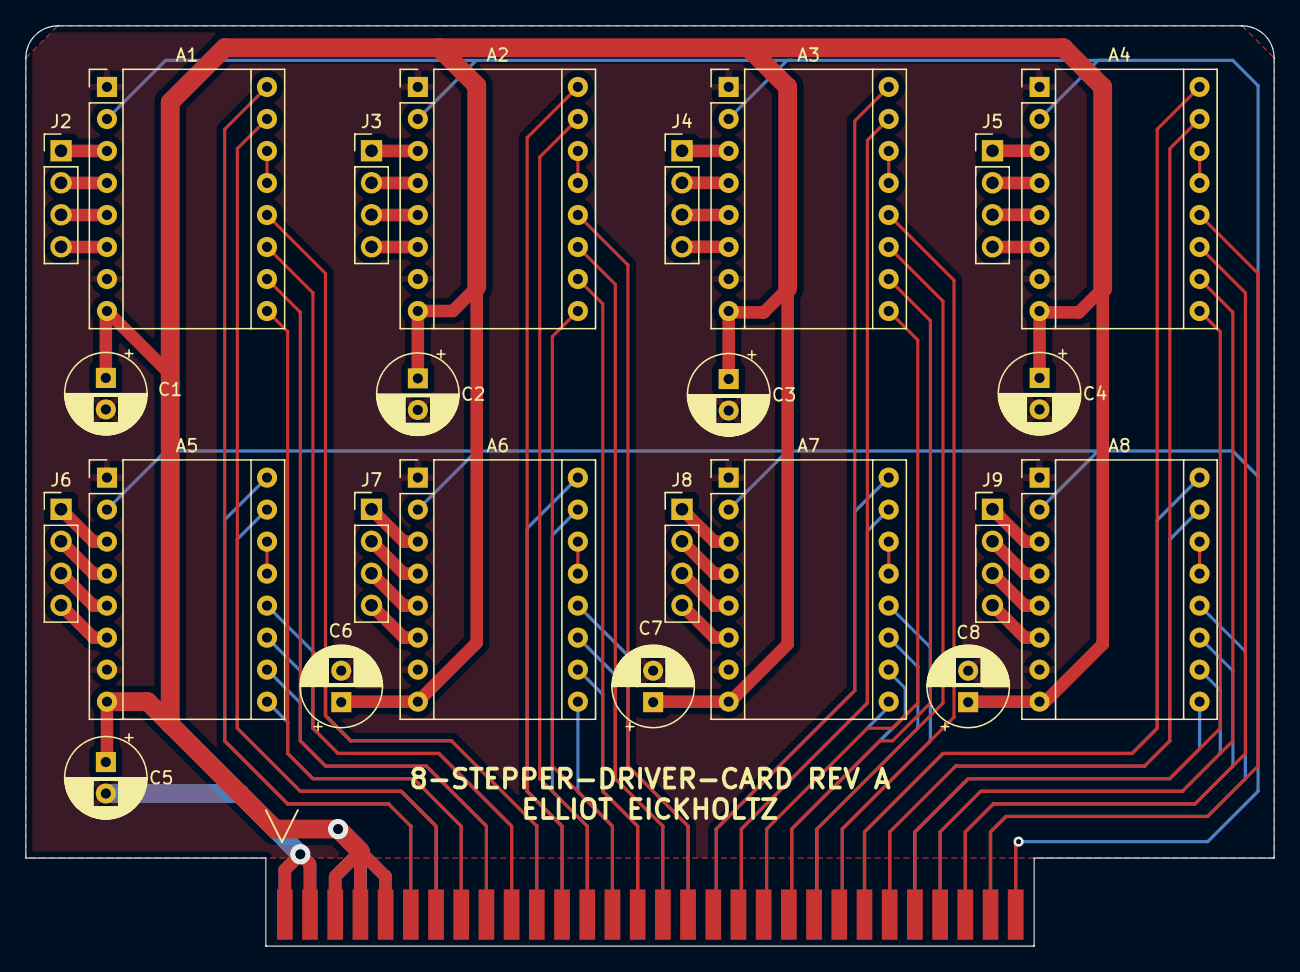
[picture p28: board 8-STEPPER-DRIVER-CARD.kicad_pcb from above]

Board: 2 copper layers, 99.1 x 73.0 mm, 25 parts (0 on the bottom side), 91 nets.

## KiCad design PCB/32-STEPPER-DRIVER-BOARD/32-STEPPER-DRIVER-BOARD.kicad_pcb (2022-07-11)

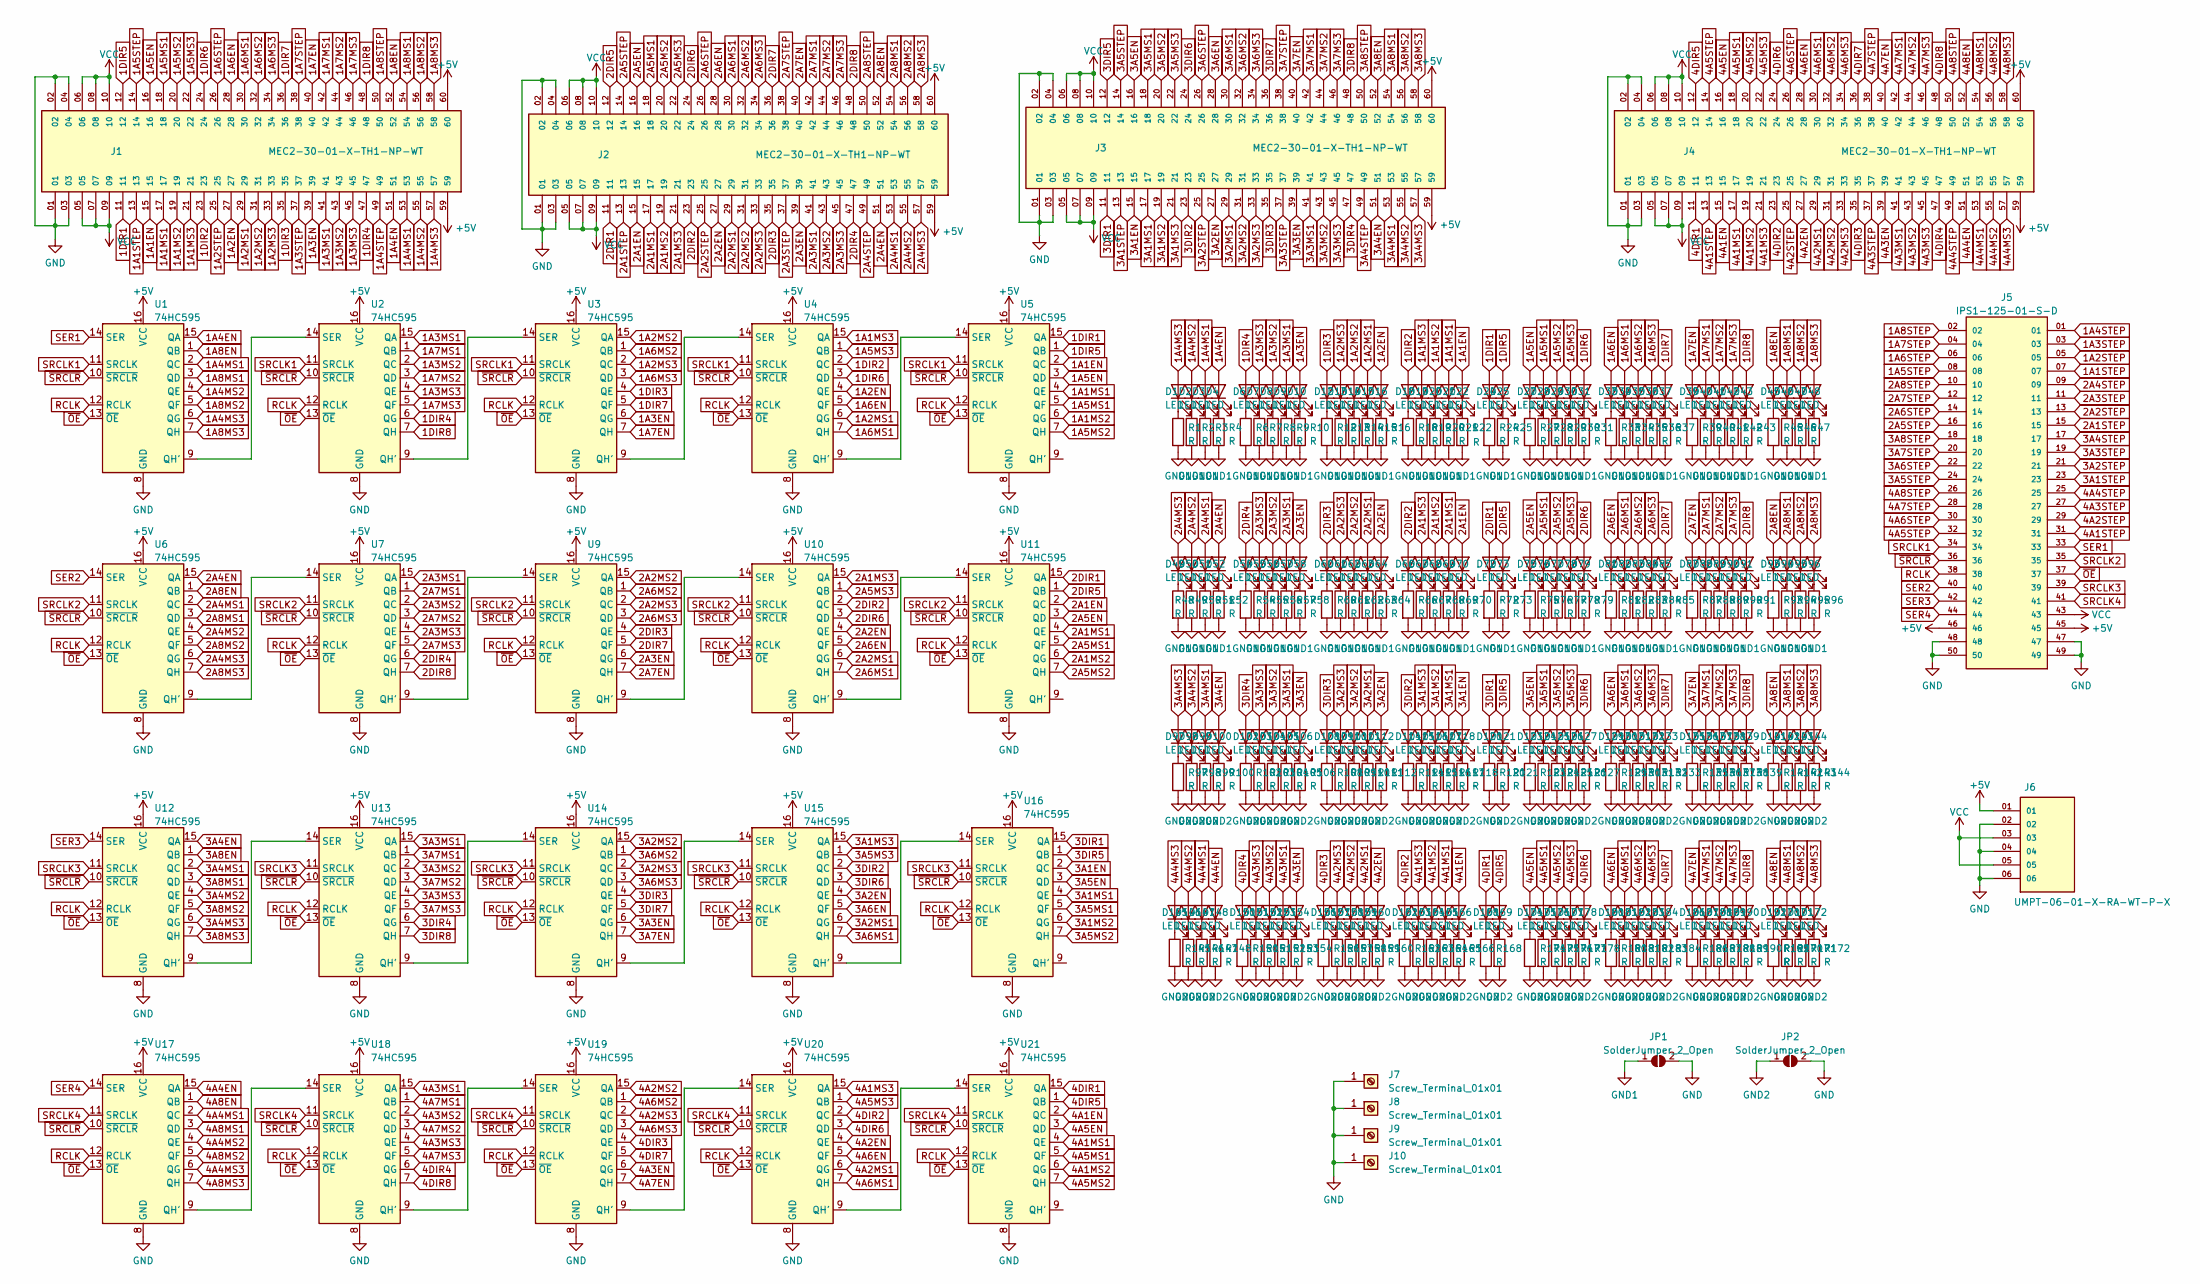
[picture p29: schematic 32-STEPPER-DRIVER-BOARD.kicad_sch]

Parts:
D1, D2, D3, D4, D6, D7, D8, D9, D10, D12, D13, D14, D15, D16, D18, D19, D20, D21, D22, D24, D25, D27, D28, D29, D30, D31, D33, D34, D35, D36, D37, D39, D40, D41, D42, D43, D45, D46, D47, D48, D49, D50, D51, D52, D54, D55, D56, D57, D58, D60, D61, D62, D63, D64, D66, D67, D68, D69, D70, D72, D73, D75, D76, D77, D78, D79, D81, D82, D83, D84, D85, D87, D88, D89, D90, D91, D93, D94, D95, D96, D97, D98, D99, D100, D102, D103, D104, D105, D106, D108, D109, D110, D111, D112, D114, D115, D116, D117, D118, D120, D121, D123, D124, D125, D126, D127, D129, D130, D131, D132, D133, D135, D136, D137, D138, D139, D141, D142, D143, D144, D145, D146, D147, D148, D150, D151, D152, D153, D154, D156, D157, D158, D159, D160, D162, D163, D164, D165, D166, D168, D169, D170, D171, D172, D174, D175, D176, D177, D178, D180, D181, D182, D183, D184, D186, D187, D188, D189, D190, D192: LED; LED_0603_1608Metric
J1, J2, J3, J4: MEC2-30-01-X-TH1-NP-WT; SAMTEC_MEC2-30-01-X-TH1-NP-WT; PARTREV F
J5: IPS1-125-01-S-D; SAMTEC_IPS1-125-01-S-D; PARTREV R
J6: UMPT-06-01-X-RA-WT-P-X; SAMTEC_UMPT-06-01-X-RA-WT-P-X; PARTREV 4
J7, J8, J9, J10: Screw_Terminal_01x01; MountingHole_2.2mm_M2_Pad
JP1, JP2: SolderJumper_2_Open; SolderJumper-2_P1.3mm_Open_RoundedPad1.0x1.5mm
R1, R2, R3, R4, R6, R7, R8, R9, R10, R12, R13, R14, R15, R16, R18, R19, R20, R21, R22, R24, R25, R27, R28, R29, R30, R31, R33, R34, R35, R36, R37, R39, R40, R41, R42, R43, R45, R46, R47, R48, R49, R50, R51, R52, R54, R55, R56, R57, R58, R60, R61, R62, R63, R64, R66, R67, R68, R69, R70, R72, R73, R75, R76, R77, R78, R79, R81, R82, R83, R84, R85, R87, R88, R89, R90, R91, R93, R94, R95, R96, R97, R98, R99, R100, R102, R103, R104, R105, R106, R108, R109, R110, R111, R112, R114, R115, R116, R117, R118, R120, R121, R123, R124, R125, R126, R127, R129, R130, R131, R132, R133, R135, R136, R137, R138, R139, R141, R142, R143, R144, R145, R146, R147, R148, R150, R151, R152, R153, R154, R156, R157, R158, R159, R160, R162, R163, R164, R165, R166, R168, R169, R170, R171, R172, R174, R175, R176, R177, R178, R180, R181, R182, R183, R184, R186, R187, R188, R189, R190, R192: R; R_0603_1608Metric
U1, U2, U3, U4, U5, U6, U7, U9, U10, U11, U12, U13, U14, U15, U16, U17, U18, U19, U20, U21: 74HC595; TSSOP-16_4.4x5mm_P0.65mm

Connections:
1A1EN: D22.2 (A), J1.15, U5.2 (QC)
1A1MS1: D21.2 (A), J1.17, U5.4 (QE)
1A1MS2: D20.2 (A), J1.19, U5.6 (QG)
1A1MS3: D19.2 (A), J1.21, U4.15 (QA)
1A1STEP: J1.13, J5.07
1A2EN: D16.2 (A), J1.27, U4.4 (QE)
1A2MS1: D15.2 (A), J1.29, U4.6 (QG)
1A2MS2: D14.2 (A), J1.31, U3.15 (QA)
1A2MS3: D13.2 (A), J1.33, U3.2 (QC)
1A2STEP: J1.25, J5.05
1A3EN: D10.2 (A), J1.39, U3.6 (QG)
1A3MS1: D9.2 (A), J1.41, U2.15 (QA)
1A3MS2: D8.2 (A), J1.43, U2.2 (QC)
1A3MS3: D7.2 (A), J1.45, U2.4 (QE)
1A3STEP: J1.37, J5.03
1A4EN: D4.2 (A), J1.51, U1.15 (QA)
1A4MS1: D3.2 (A), J1.53, U1.2 (QC)
1A4MS2: D2.2 (A), J1.55, U1.4 (QE)
1A4MS3: D1.2 (A), J1.57, U1.6 (QG)
1A4STEP: J1.49, J5.01
1A5EN: D27.2 (A), J1.16, U5.3 (QD)
1A5MS1: D28.2 (A), J1.18, U5.5 (QF)
1A5MS2: D29.2 (A), J1.20, U5.7 (QH)
1A5MS3: D30.2 (A), J1.22, U4.1 (QB)
1A5STEP: J1.14, J5.08
1A6EN: D33.2 (A), J1.28, U4.5 (QF)
1A6MS1: D34.2 (A), J1.30, U4.7 (QH)
1A6MS2: D35.2 (A), J1.32, U3.1 (QB)
1A6MS3: D36.2 (A), J1.34, U3.3 (QD)
1A6STEP: J1.26, J5.06
1A7EN: D39.2 (A), J1.40, U3.7 (QH)
1A7MS1: D40.2 (A), J1.42, U2.1 (QB)
1A7MS2: D41.2 (A), J1.44, U2.3 (QD)
1A7MS3: D42.2 (A), J1.46, U2.5 (QF)
1A7STEP: J1.38, J5.04
1A8EN: D45.2 (A), J1.52, U1.1 (QB)
1A8MS1: D46.2 (A), J1.54, U1.3 (QD)
1A8MS2: D47.2 (A), J1.56, U1.5 (QF)
1A8MS3: D48.2 (A), J1.58, U1.7 (QH)
1A8STEP: J1.50, J5.02
1DIR1: D24.2 (A), J1.11, U5.15 (QA)
1DIR2: D18.2 (A), J1.23, U4.2 (QC)
1DIR3: D12.2 (A), J1.35, U3.4 (QE)
1DIR4: D6.2 (A), J1.47, U2.6 (QG)
1DIR5: D25.2 (A), J1.12, U5.1 (QB)
1DIR6: D31.2 (A), J1.24, U4.3 (QD)
1DIR7: D37.2 (A), J1.36, U3.5 (QF)
1DIR8: D43.2 (A), J1.48, U2.7 (QH)
2A1EN: D70.2 (A), J2.15, U11.2 (QC)
2A1MS1: D69.2 (A), J2.17, U11.4 (QE)
2A1MS2: D68.2 (A), J2.19, U11.6 (QG)
2A1MS3: D67.2 (A), J2.21, U10.15 (QA)
2A1STEP: J2.13, J5.15
2A2EN: D64.2 (A), J2.27, U10.4 (QE)
2A2MS1: D63.2 (A), J2.29, U10.6 (QG)
2A2MS2: D62.2 (A), J2.31, U9.15 (QA)
2A2MS3: D61.2 (A), J2.33, U9.2 (QC)
2A2STEP: J2.25, J5.13
2A3EN: D58.2 (A), J2.39, U9.6 (QG)
2A3MS1: D57.2 (A), J2.41, U7.15 (QA)
2A3MS2: D56.2 (A), J2.43, U7.2 (QC)
2A3MS3: D55.2 (A), J2.45, U7.4 (QE)
2A3STEP: J2.37, J5.11
2A4EN: D52.2 (A), J2.51, U6.15 (QA)
2A4MS1: D51.2 (A), J2.53, U6.2 (QC)
2A4MS2: D50.2 (A), J2.55, U6.4 (QE)
2A4MS3: D49.2 (A), J2.57, U6.6 (QG)
2A4STEP: J2.49, J5.09
2A5EN: D75.2 (A), J2.16, U11.3 (QD)
2A5MS1: D76.2 (A), J2.18, U11.5 (QF)
2A5MS2: D77.2 (A), J2.20, U11.7 (QH)
2A5MS3: D78.2 (A), J2.22, U10.1 (QB)
2A5STEP: J2.14, J5.16
2A6EN: D81.2 (A), J2.28, U10.5 (QF)
2A6MS1: D82.2 (A), J2.30, U10.7 (QH)
2A6MS2: D83.2 (A), J2.32, U9.1 (QB)
2A6MS3: D84.2 (A), J2.34, U9.3 (QD)
2A6STEP: J2.26, J5.14
2A7EN: D87.2 (A), J2.40, U9.7 (QH)
2A7MS1: D88.2 (A), J2.42, U7.1 (QB)
2A7MS2: D89.2 (A), J2.44, U7.3 (QD)
2A7MS3: D90.2 (A), J2.46, U7.5 (QF)
2A7STEP: J2.38, J5.12
2A8EN: D93.2 (A), J2.52, U6.1 (QB)
2A8MS1: D94.2 (A), J2.54, U6.3 (QD)
2A8MS2: D95.2 (A), J2.56, U6.5 (QF)
2A8MS3: D96.2 (A), J2.58, U6.7 (QH)
2A8STEP: J2.50, J5.10
2DIR1: D72.2 (A), J2.11, U11.15 (QA)
2DIR2: D66.2 (A), J2.23, U10.2 (QC)
2DIR3: D60.2 (A), J2.35, U9.4 (QE)
2DIR4: D54.2 (A), J2.47, U7.6 (QG)
2DIR5: D73.2 (A), J2.12, U11.1 (QB)
2DIR6: D79.2 (A), J2.24, U10.3 (QD)
2DIR7: D85.2 (A), J2.36, U9.5 (QF)
2DIR8: D91.2 (A), J2.48, U7.7 (QH)
3A1EN: D118.2 (A), J3.15, U16.2 (QC)
3A1MS1: D117.2 (A), J3.17, U16.4 (QE)
3A1MS2: D116.2 (A), J3.19, U16.6 (QG)
3A1MS3: D115.2 (A), J3.21, U15.15 (QA)
3A1STEP: J3.13, J5.23
3A2EN: D112.2 (A), J3.27, U15.4 (QE)
3A2MS1: D111.2 (A), J3.29, U15.6 (QG)
3A2MS2: D110.2 (A), J3.31, U14.15 (QA)
3A2MS3: D109.2 (A), J3.33, U14.2 (QC)
3A2STEP: J3.25, J5.21
3A3EN: D106.2 (A), J3.39, U14.6 (QG)
3A3MS1: D105.2 (A), J3.41, U13.15 (QA)
3A3MS2: D104.2 (A), J3.43, U13.2 (QC)
3A3MS3: D103.2 (A), J3.45, U13.4 (QE)
3A3STEP: J3.37, J5.19
3A4EN: D100.2 (A), J3.51, U12.15 (QA)
3A4MS1: D99.2 (A), J3.53, U12.2 (QC)
3A4MS2: D98.2 (A), J3.55, U12.4 (QE)
3A4MS3: D97.2 (A), J3.57, U12.6 (QG)
3A4STEP: J3.49, J5.17
3A5EN: D123.2 (A), J3.16, U16.3 (QD)
3A5MS1: D124.2 (A), J3.18, U16.5 (QF)
3A5MS2: D125.2 (A), J3.20, U16.7 (QH)
3A5MS3: D126.2 (A), J3.22, U15.1 (QB)
3A5STEP: J3.14, J5.24
3A6EN: D129.2 (A), J3.28, U15.5 (QF)
3A6MS1: D130.2 (A), J3.30, U15.7 (QH)
3A6MS2: D131.2 (A), J3.32, U14.1 (QB)
3A6MS3: D132.2 (A), J3.34, U14.3 (QD)
3A6STEP: J3.26, J5.22
3A7EN: D135.2 (A), J3.40, U14.7 (QH)
3A7MS1: D136.2 (A), J3.42, U13.1 (QB)
3A7MS2: D137.2 (A), J3.44, U13.3 (QD)
3A7MS3: D138.2 (A), J3.46, U13.5 (QF)
3A7STEP: J3.38, J5.20
3A8EN: D141.2 (A), J3.52, U12.1 (QB)
3A8MS1: D142.2 (A), J3.54, U12.3 (QD)
3A8MS2: D143.2 (A), J3.56, U12.5 (QF)
3A8MS3: D144.2 (A), J3.58, U12.7 (QH)
3A8STEP: J3.50, J5.18
3DIR1: D120.2 (A), J3.11, U16.15 (QA)
3DIR2: D114.2 (A), J3.23, U15.2 (QC)
3DIR3: D108.2 (A), J3.35, U14.4 (QE)
3DIR4: D102.2 (A), J3.47, U13.6 (QG)
3DIR5: D121.2 (A), J3.12, U16.1 (QB)
3DIR6: D127.2 (A), J3.24, U15.3 (QD)
3DIR7: D133.2 (A), J3.36, U14.5 (QF)
3DIR8: D139.2 (A), J3.48, U13.7 (QH)
4A1EN: D166.2 (A), J4.15, U21.2 (QC)
4A1MS1: D165.2 (A), J4.17, U21.4 (QE)
4A1MS2: D164.2 (A), J4.19, U21.6 (QG)
4A1MS3: D163.2 (A), J4.21, U20.15 (QA)
4A1STEP: J4.13, J5.31
4A2EN: D160.2 (A), J4.27, U20.4 (QE)
4A2MS1: D159.2 (A), J4.29, U20.6 (QG)
4A2MS2: D158.2 (A), J4.31, U19.15 (QA)
4A2MS3: D157.2 (A), J4.33, U19.2 (QC)
4A2STEP: J4.25, J5.29
4A3EN: D154.2 (A), J4.39, U19.6 (QG)
4A3MS1: D153.2 (A), J4.41, U18.15 (QA)
4A3MS2: D152.2 (A), J4.43, U18.2 (QC)
4A3MS3: D151.2 (A), J4.45, U18.4 (QE)
4A3STEP: J4.37, J5.27
4A4EN: D148.2 (A), J4.51, U17.15 (QA)
4A4MS1: D147.2 (A), J4.53, U17.2 (QC)
4A4MS2: D146.2 (A), J4.55, U17.4 (QE)
4A4MS3: D145.2 (A), J4.57, U17.6 (QG)
4A4STEP: J4.49, J5.25
4A5EN: D174.2 (A), J4.16, U21.3 (QD)
4A5MS1: D175.2 (A), J4.18, U21.5 (QF)
4A5MS2: D176.2 (A), J4.20, U21.7 (QH)
4A5MS3: D177.2 (A), J4.22, U20.1 (QB)
4A5STEP: J4.14, J5.32
4A6EN: D180.2 (A), J4.28, U20.5 (QF)
4A6MS1: D181.2 (A), J4.30, U20.7 (QH)
4A6MS2: D182.2 (A), J4.32, U19.1 (QB)
4A6MS3: D183.2 (A), J4.34, U19.3 (QD)
4A6STEP: J4.26, J5.30
4A7EN: D186.2 (A), J4.40, U19.7 (QH)
4A7MS1: D187.2 (A), J4.42, U18.1 (QB)
4A7MS2: D188.2 (A), J4.44, U18.3 (QD)
4A7MS3: D189.2 (A), J4.46, U18.5 (QF)
4A7STEP: J4.38, J5.28
4A8EN: D192.2 (A), J4.52, U17.1 (QB)
4A8MS1: D170.2 (A), J4.54, U17.3 (QD)
4A8MS2: D171.2 (A), J4.56, U17.5 (QF)
4A8MS3: D172.2 (A), J4.58, U17.7 (QH)
4A8STEP: J4.50, J5.26
4DIR1: D168.2 (A), J4.11, U21.15 (QA)
4DIR2: D162.2 (A), J4.23, U20.2 (QC)
4DIR3: D156.2 (A), J4.35, U19.4 (QE)
4DIR4: D150.2 (A), J4.47, U18.6 (QG)
4DIR5: D169.2 (A), J4.12, U21.1 (QB)
4DIR6: D178.2 (A), J4.24, U20.3 (QD)
4DIR7: D184.2 (A), J4.36, U19.5 (QF)
4DIR8: D190.2 (A), J4.48, U18.7 (QH)
+5V: J1.59, J1.60, J2.59, J2.60, J3.59, J3.60, J4.59, J4.60, J5.45, J5.46, J6.01, U1.16 (VCC), U2.16 (VCC), U3.16 (VCC), U4.16 (VCC), U5.16 (VCC), U6.16 (VCC), U7.16 (VCC), U9.16 (VCC), U10.16 (VCC), U11.16 (VCC), U12.16 (VCC), U13.16 (VCC), U14.16 (VCC), U15.16 (VCC), U16.16 (VCC), U17.16 (VCC), U18.16 (VCC), U19.16 (VCC), U20.16 (VCC), U21.16 (VCC)
GND: J1.01, J1.02, J1.03, J1.04, J2.01, J2.02, J2.03, J2.04, J3.01, J3.02, J3.03, J3.04, J4.01, J4.02, J4.03, J4.04, J5.47, J5.48, J5.49, J5.50, J6.02, J6.04, J6.06, J7.1, J8.1, J9.1, J10.1, JP1.2 (B), JP2.2 (B), U1.8 (GND), U2.8 (GND), U3.8 (GND), U4.8 (GND), U5.8 (GND), U6.8 (GND), U7.8 (GND), U9.8 (GND), U10.8 (GND), U11.8 (GND), U12.8 (GND), U13.8 (GND), U14.8 (GND), U15.8 (GND), U16.8 (GND), U17.8 (GND), U18.8 (GND), U19.8 (GND), U20.8 (GND), U21.8 (GND)
GND1: JP1.1 (A), R1.2, R2.2, R3.2, R4.2, R6.2, R7.2, R8.2, R9.2, R10.2, R12.2, R13.2, R14.2, R15.2, R16.2, R18.2, R19.2, R20.2, R21.2, R22.2, R24.2, R25.2, R27.2, R28.2, R29.2, R30.2, R31.2, R33.2, R34.2, R35.2, R36.2, R37.2, R39.2, R40.2, R41.2, R42.2, R43.2, R45.2, R46.2, R47.2, R48.2, R49.2, R50.2, R51.2, R52.2, R54.2, R55.2, R56.2, R57.2, R58.2, R60.2, R61.2, R62.2, R63.2, R64.2, R66.2, R67.2, R68.2, R69.2, R70.2, R72.2, R73.2, R75.2, R76.2, R77.2, R78.2, R79.2, R81.2, R82.2, R83.2, R84.2, R85.2, R87.2, R88.2, R89.2, R90.2, R91.2, R93.2, R94.2, R95.2, R96.2
GND2: JP2.1 (A), R97.2, R98.2, R99.2, R100.2, R102.2, R103.2, R104.2, R105.2, R106.2, R108.2, R109.2, R110.2, R111.2, R112.2, R114.2, R115.2, R116.2, R117.2, R118.2, R120.2, R121.2, R123.2, R124.2, R125.2, R126.2, R127.2, R129.2, R130.2, R131.2, R132.2, R133.2, R135.2, R136.2, R137.2, R138.2, R139.2, R141.2, R142.2, R143.2, R144.2, R145.2, R146.2, R147.2, R148.2, R150.2, R151.2, R152.2, R153.2, R154.2, R156.2, R157.2, R158.2, R159.2, R160.2, R162.2, R163.2, R164.2, R165.2, R166.2, R168.2, R169.2, R170.2, R171.2, R172.2, R174.2, R175.2, R176.2, R177.2, R178.2, R180.2, R181.2, R182.2, R183.2, R184.2, R186.2, R187.2, R188.2, R189.2, R190.2, R192.2
unnamed: D1.1 (K), R1.1
unnamed: D2.1 (K), R2.1
unnamed: D3.1 (K), R3.1
unnamed: D4.1 (K), R4.1
unnamed: D6.1 (K), R6.1
unnamed: D7.1 (K), R7.1
unnamed: D8.1 (K), R8.1
unnamed: D9.1 (K), R9.1
unnamed: D10.1 (K), R10.1
unnamed: D12.1 (K), R12.1
unnamed: D13.1 (K), R13.1
unnamed: D14.1 (K), R14.1
unnamed: D15.1 (K), R15.1
unnamed: D16.1 (K), R16.1
unnamed: D18.1 (K), R18.1
unnamed: D19.1 (K), R19.1
unnamed: D20.1 (K), R20.1
unnamed: D21.1 (K), R21.1
unnamed: D22.1 (K), R22.1
unnamed: D24.1 (K), R24.1
unnamed: D25.1 (K), R25.1
unnamed: D27.1 (K), R27.1
unnamed: D28.1 (K), R28.1
unnamed: D29.1 (K), R29.1
unnamed: D30.1 (K), R30.1
unnamed: D31.1 (K), R31.1
unnamed: D33.1 (K), R33.1
unnamed: D34.1 (K), R34.1
unnamed: D35.1 (K), R35.1
unnamed: D36.1 (K), R36.1
unnamed: D37.1 (K), R37.1
unnamed: D39.1 (K), R39.1
unnamed: D40.1 (K), R40.1
unnamed: D41.1 (K), R41.1
unnamed: D42.1 (K), R42.1
unnamed: D43.1 (K), R43.1
unnamed: D45.1 (K), R45.1
unnamed: D46.1 (K), R46.1
unnamed: D47.1 (K), R47.1
unnamed: D48.1 (K), R48.1
unnamed: D49.1 (K), R49.1
unnamed: D50.1 (K), R50.1
unnamed: D51.1 (K), R51.1
unnamed: D52.1 (K), R52.1
unnamed: D54.1 (K), R54.1
unnamed: D55.1 (K), R55.1
unnamed: D56.1 (K), R56.1
unnamed: D57.1 (K), R57.1
unnamed: D58.1 (K), R58.1
unnamed: D60.1 (K), R60.1
unnamed: D61.1 (K), R61.1
unnamed: D62.1 (K), R62.1
unnamed: D63.1 (K), R63.1
unnamed: D64.1 (K), R64.1
unnamed: D66.1 (K), R66.1
unnamed: D67.1 (K), R67.1
unnamed: D68.1 (K), R68.1
unnamed: D69.1 (K), R69.1
unnamed: D70.1 (K), R70.1
unnamed: D72.1 (K), R72.1
unnamed: D73.1 (K), R73.1
unnamed: D75.1 (K), R75.1
unnamed: D76.1 (K), R76.1
unnamed: D77.1 (K), R77.1
unnamed: D78.1 (K), R78.1
unnamed: D79.1 (K), R79.1
unnamed: D81.1 (K), R81.1
unnamed: D82.1 (K), R82.1
unnamed: D83.1 (K), R83.1
unnamed: D84.1 (K), R84.1
unnamed: D85.1 (K), R85.1
unnamed: D87.1 (K), R87.1
unnamed: D88.1 (K), R88.1
unnamed: D89.1 (K), R89.1
unnamed: D90.1 (K), R90.1
unnamed: D91.1 (K), R91.1
unnamed: D93.1 (K), R93.1
unnamed: D94.1 (K), R94.1
unnamed: D95.1 (K), R95.1
unnamed: D96.1 (K), R96.1
unnamed: D97.1 (K), R97.1
unnamed: D98.1 (K), R98.1
unnamed: D99.1 (K), R99.1
unnamed: D100.1 (K), R100.1
unnamed: D102.1 (K), R102.1
unnamed: D103.1 (K), R103.1
unnamed: D104.1 (K), R104.1
unnamed: D105.1 (K), R105.1
unnamed: D106.1 (K), R106.1
unnamed: D108.1 (K), R108.1
unnamed: D109.1 (K), R109.1
unnamed: D110.1 (K), R110.1
unnamed: D111.1 (K), R111.1
unnamed: D112.1 (K), R112.1
unnamed: D114.1 (K), R114.1
unnamed: D115.1 (K), R115.1
unnamed: D116.1 (K), R116.1
unnamed: D117.1 (K), R117.1
unnamed: D118.1 (K), R118.1
unnamed: D120.1 (K), R120.1
unnamed: D121.1 (K), R121.1
unnamed: D123.1 (K), R123.1
unnamed: D124.1 (K), R124.1
unnamed: D125.1 (K), R125.1
unnamed: D126.1 (K), R126.1
unnamed: D127.1 (K), R127.1
unnamed: D129.1 (K), R129.1
unnamed: D130.1 (K), R130.1
unnamed: D131.1 (K), R131.1
unnamed: D132.1 (K), R132.1
unnamed: D133.1 (K), R133.1
unnamed: D135.1 (K), R135.1
unnamed: D136.1 (K), R136.1
unnamed: D137.1 (K), R137.1
unnamed: D138.1 (K), R138.1
unnamed: D139.1 (K), R139.1
unnamed: D141.1 (K), R141.1
unnamed: D142.1 (K), R142.1
unnamed: D143.1 (K), R143.1
unnamed: D144.1 (K), R144.1
unnamed: D145.1 (K), R145.1
unnamed: D146.1 (K), R146.1
unnamed: D147.1 (K), R147.1
unnamed: D148.1 (K), R148.1
unnamed: D150.1 (K), R150.1
unnamed: D151.1 (K), R151.1
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

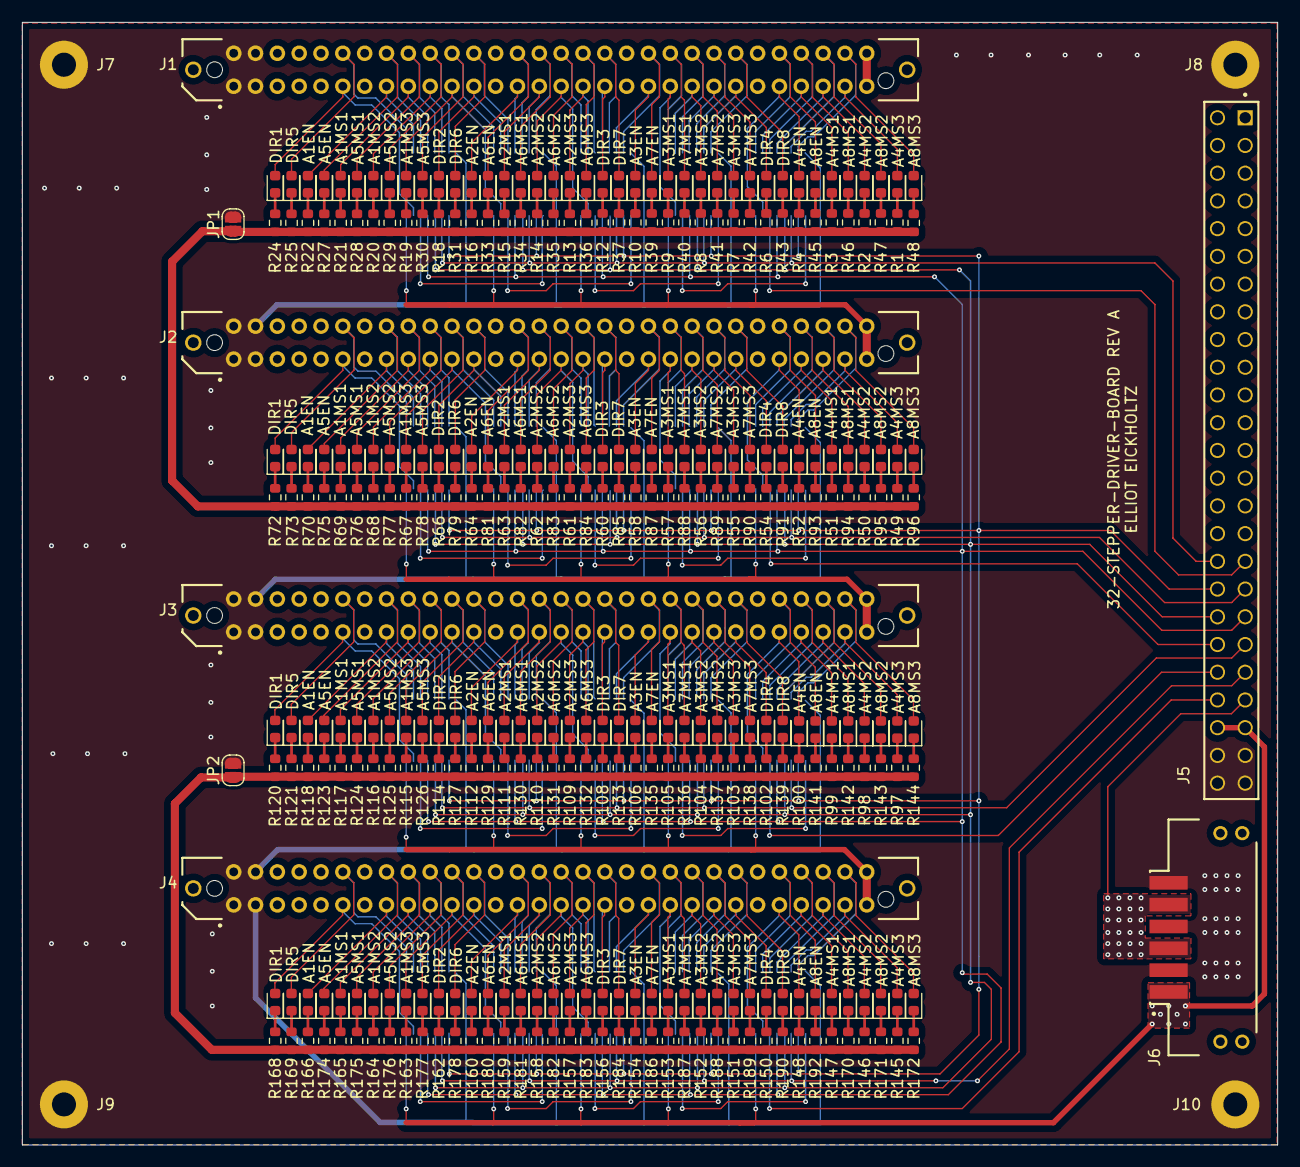
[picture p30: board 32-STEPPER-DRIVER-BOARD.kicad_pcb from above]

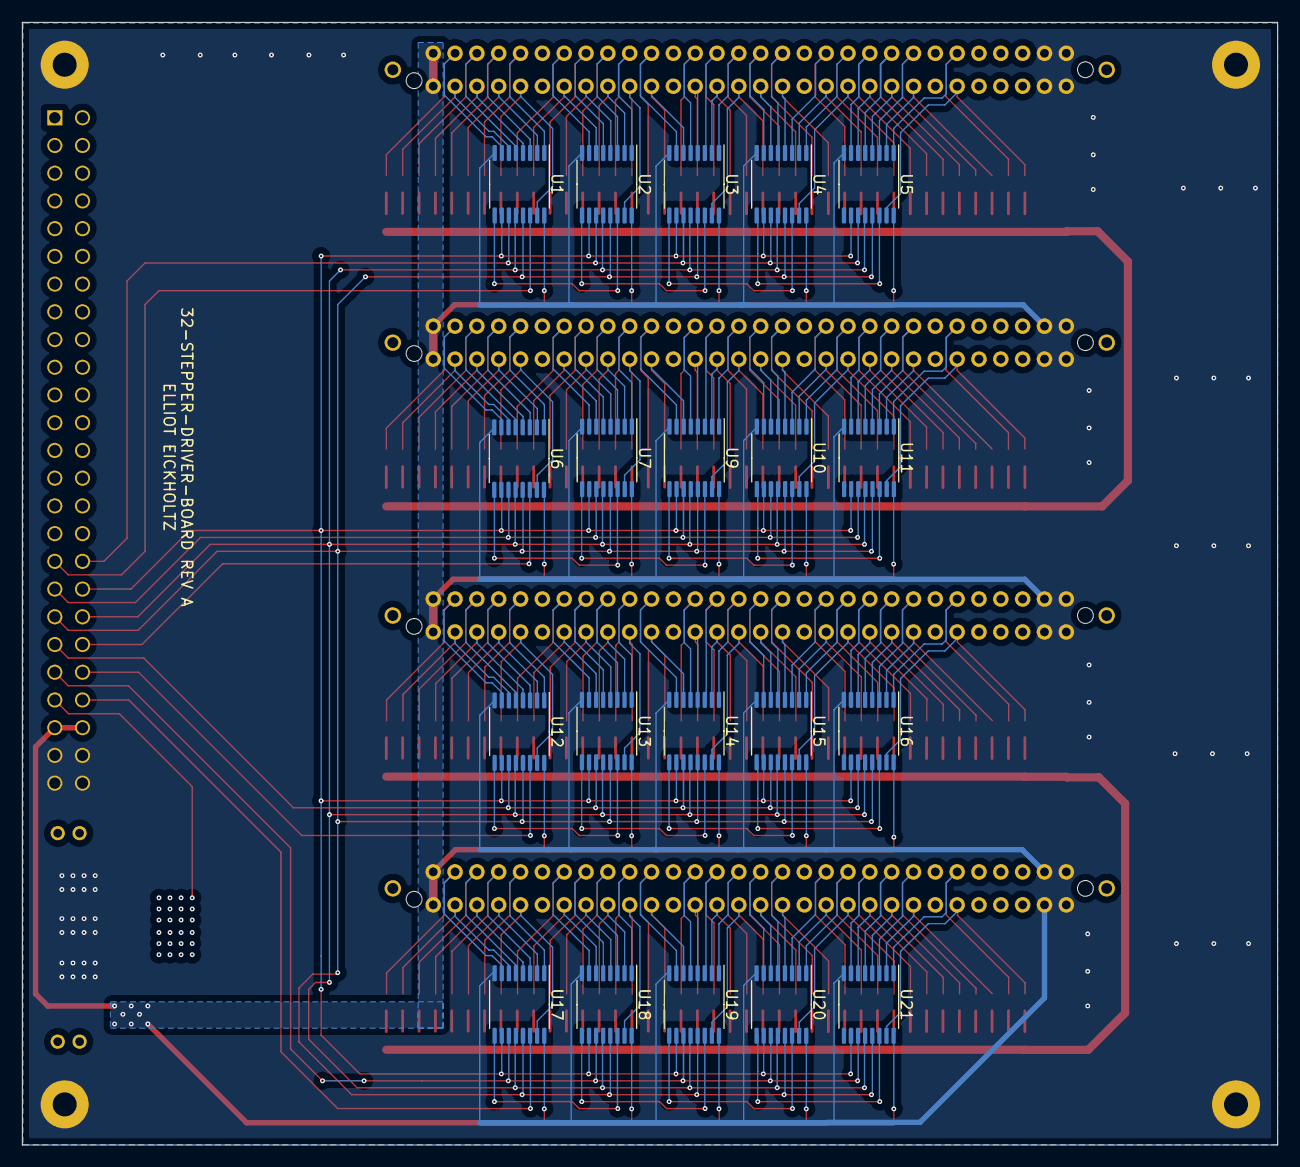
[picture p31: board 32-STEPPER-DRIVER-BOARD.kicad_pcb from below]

Board: 4 copper layers, 115.0 x 102.8 mm, 352 parts (20 on the bottom side), 384 nets.

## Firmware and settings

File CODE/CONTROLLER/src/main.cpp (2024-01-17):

/*
 * File name: main.cpp -> CONTROLLER
 * Project: 64 Motor Driver
 * Author: Elliot Eickholtz
 * Purpose: Master controller to 2 slave Teensy 4.0's, 40 shift registers, and LED lighting. 
 * Custom com protocol used for communication over USB and serial busses.
 * 
*/

#include <Arduino.h>
#include "Music_Serial.h"
#include "Shift_Control.h"
#include "Light_Control.h"

MainControl Control(1);


void OnNoteOff(byte channel, byte note, byte velocity)
{
    !DEBUG ? true : Serial.print("channel On: ");Serial.println(channel);
    Control.midiEvent(channel, note, velocity);
}

void OnNoteOn(byte channel, byte note, byte velocity)
{
    !DEBUG ? true : Serial.print("channel Off: ");Serial.println(channel);
    Control.midiEvent(channel, note, velocity);
}

void OnControlChange(byte channel, byte number, byte value)
{
    Serial.println("--Control change--");
    Serial.print("Channel: ");Serial.println(channel);
    Serial.print("Number: ");Serial.println(number);
    Serial.print("Value: ");Serial.println(value);
    Control.controlEvent(channel, number, value);
}

void setup()
{
    Serial.begin(115200);

    usbMIDI.setHandleNoteOff(OnNoteOff);
    usbMIDI.setHandleNoteOn(OnNoteOn);
    usbMIDI.setHandleControlChange(OnControlChange);

    leds.begin();
    leds.show();
    delay(3000);
}

void loop()
{
    usbMIDI.read();
    // Control.midiEvent(1, 36, 100);
    // delay(500);
    // Control.midiEvent(1, 48, 100);
    // delay(500);
    // Control.midiEvent(1, 60, 100);
    // delay(500);
    // Control.midiEvent(1, 36, 0);
    // delay(500);
    // Control.midiEvent(1, 48, 0);
    // delay(500);
    // Control.midiEvent(1, 60, 0);
    // delay(500);
}

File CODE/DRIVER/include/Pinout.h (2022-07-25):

/*
 * File name: Pinout.h -> DRIVER
 * Project: 64 Motor Driver
 * Author: Elliot Eickholtz
 * Purpose: Define all pins used on the Teensy 4.0.
 * 
*/

#ifndef PINOUT_H
#define PINOUT_H

//  *Initialize all stepper driver freq pins to a unique identifier*  //
//  *--------------------------------------------------------------*  //
#define A1STEP1 6 
#define A2STEP1 4 
#define A3STEP1 2 
#define A4STEP1 0 
#define A5STEP1 9 
#define A6STEP1 5 
#define A7STEP1 3 
#define A8STEP1 1 
#define A1STEP2 31
#define A2STEP2 33
#define A3STEP2 12
#define A4STEP2 10
#define A5STEP2 28
#define A6STEP2 30
#define A7STEP2 32
#define A8STEP2 11
#define A1STEP3 13
#define A2STEP3 25
#define A3STEP3 27
#define A4STEP3 29
#define A5STEP3 15
#define A6STEP3 14
#define A7STEP3 24
#define A8STEP3 26
#define A1STEP4 22
#define A2STEP4 20
#define A3STEP4 18
#define A4STEP4 16
#define A5STEP4 23
#define A6STEP4 21
#define A7STEP4 19
#define A8STEP4 17

//  *^^^^^^^^^^^^^^^^^^^^^^^^^^^^^^^^^^^^^^^^^^^^^^^^^^^^^^^^^^^^^^*  //

#endif  // PINOUT_H

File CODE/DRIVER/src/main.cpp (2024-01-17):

/*
 * File name: main.cpp -> DRIVER
 * Project: 64 Motor Driver
 * Author: Elliot Eickholtz
 * Purpose: Drive 64 stepper motors with 2 Teensy 4.0's, 32 motors each. Slave to Teensy 4.1 microcontroller.
 * 
*/

//* Library includes *//
#include <Arduino.h>
#include <Stepper_Music.h>
#include <Music_Serial.h>
//*^^^^^^^^^^^^^^^^^^*//

// Initialize Class, "1" means nothing.
Music_Serial Master(1);

void setup() 
{
	Serial.begin(115200);
	Master.serialInit();
}

void loop() {
  	if(Master.available()) 
	{
		// Read Serial buffer from master
		Master.read();
		// Decode and set master command into action
		Master.setMasterCommand();
	}

	// Loop through all 32 motors tied to microcontroller
  	for(int i=0; i<32; i++)
  	{
		// Wait the alloted time to replicate set frequency
		if(AllMotors[i].pulseWait[0] || AllMotors[i].pulseWait[1] || AllMotors[i].pulseWait[2] || AllMotors[i].pulseWait[3])
		{
			AllMotors[i].singleStep();
		}
  	}
}

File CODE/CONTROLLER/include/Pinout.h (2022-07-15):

/*
 * File name: Pinout.h -> CONTROLLER
 * Project: 64 Motor Driver
 * Author: Elliot Eickholtz
 * Purpose: Define all pins used on the Teensy 4.1.
 * 
*/

#ifndef PINOUT_H
#define PINOUT_H

//  *Initialize all stepper driver freq pins to a unique identifier*  //
//  *--------------------------------------------------------------*  //

// Latch clock
#define RCLK1 26
#define RCLK2 18

// Data in
#define SER1 10
#define SER2 24
#define SER3 40
#define SER4 33

#define SER5 23
#define SER6 16
#define SER7 14
#define SER8 9

// Shift clock
#define SRCLK1 32
#define SRCLK2 31
#define SRCLK3 25
#define SRCLK4 41

#define SRCLK5 22
#define SRCLK6 21
#define SRCLK7 17
#define SRCLK8 15

// Reset
#define SRCLR1 30
#define SRCLR2 20

// Output enable
#define OE1 27
#define OE2 19

//  *^^^^^^^^^^^^^^^^^^^^^^^^^^^^^^^^^^^^^^^^^^^^^^^^^^^^^^^^^^^^^^*  //

//  *Define shift register pin order*   //
//  *-------------------------------*   //

#define DIR01 1
#define DIR05 2
#define A01EN 3
#define A05EN 4
#define A1MS1 5
#define A5MS1 6
#define A1MS2 7
#define A5MS2 8
#define A1MS3 9
#define A5MS3 10
#define DIR02 11
#define DIR06 12
#define A02EN 13
#define A06EN 14
#define A2MS1 15
#define A6MS1 16
#define A2MS2 17
#define A6MS2 18
#define A2MS3 19
#define A6MS3 20
#define DIR03 21
#define DIR07 22
#define A03EN 23
#define A07EN 24
#define A3MS1 25
#define A7MS1 26
#define A3MS2 27
#define A7MS2 28
#define A3MS3 29
#define A7MS3 30
#define DIR04 31
#define DIR08 32
#define A04EN 33
#define A08EN 34
#define A4MS1 35
#define A8MS1 36
#define A4MS2 37
#define A8MS2 38
#define A4MS3 39
#define A8MS3 40

uint8_t enablePins[8] = {A01EN, A02EN, A03EN, A04EN, A05EN, A06EN, A07EN, A08EN};
uint8_t directionPins[8] = {DIR01, DIR02, DIR03, DIR04, DIR05, DIR06, DIR07, DIR08};
uint8_t MS1Pins[8] = {A1MS1, A2MS1, A3MS1, A4MS1, A5MS1, A6MS1, A7MS1, A8MS1};
uint8_t MS2Pins[8] = {A1MS2, A2MS2, A3MS2, A4MS2, A5MS2, A6MS2, A7MS2, A8MS2};
uint8_t MS3Pins[8] = {A1MS3, A2MS3, A3MS3, A4MS3, A5MS3, A6MS3, A7MS3, A8MS3};

//  *^^^^^^^^^^^^^^^^^^^^^^^^^^^^^^^*   //

#endif  // PINOUT_H

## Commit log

2022-05-06 initial commit
    Contains initial conceptual dwg
    [64_MOTOR_CONCEPTUAL.dwg]
2022-05-07 minimal change
    [64_MOTOR_CONCEPTUAL.dwg]
2022-05-12 Concept #2 added
    [64_MOTOR_CONCEPTUAL.dwg]
2022-05-12 SECOND CONCEPT ADDED TO
    [64_MOTOR_CONCEPTUAL.dwg]
2022-05-12 File and folder project setup
    Based off of 2nd conceptual design
    [16-STEPPER-DRIVER-CARD.kicad_pcb, 16-STEPPER-DRIVER-CARD.kicad_sch, 32-STEPPER-DRIVER-BOARD.kicad_pcb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]
2022-05-14 initial schematic layout
    [16-STEPPER-DRIVER-CARD.kicad_sch, 32-STEPPER-DRIVER-BOARD.kicad_sch, 64-STEPPER-CONTROLLER.kicad_sch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]
2022-05-17 PCB Routing for Stepper Card
    [16-STEPPER-DRIVER-CARD.kicad_pcb, 16-STEPPER-DRIVER-CARD.kicad_sch]
2022-05-18 begin 32 stepper board
    [32-STEPPER-DRIVER-BOARD.kicad_sch]
2022-05-18 final rev 1 design, no slots
    [16-STEPPER-DRIVER-CARD.kicad_pcb]
2022-05-18 Name change, final addition before prototype order
    [8-STEPPER-DRIVER-CARD-B_Cu.gbl, 8-STEPPER-DRIVER-CARD-B_Mask.gbs, 8-STEPPER-DRIVER-CARD-B_Paste.gbp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]
2022-05-18 folder name change
    [8-STEPPER-DRIVER-CARD-B_Cu.gbl, 8-STEPPER-DRIVER-CARD-B_Mask.gbs, 8-STEPPER-DRIVER-CARD-B_Paste.gbp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]
2022-05-19 initial 32-driver layout
    [32-STEPPER-DRIVER-BOARD.kicad_pcb, 32-STEPPER-DRIVER-BOARD.kicad_sch]
2022-05-19 MORE 32-STEPPER LAYOUT WORK
    [32-STEPPER-DRIVER-BOARD.kicad_pcb]
2022-05-23 added more connectors
    [32-STEPPER-DRIVER-BOARD.kicad_pcb, 32-STEPPER-DRIVER-BOARD.kicad_sch]
2022-05-25 LED's and resistors placed
    [32-STEPPER-DRIVER-BOARD.kicad_pcb]
2022-05-27 re-routing bottom layer
    [32-STEPPER-DRIVER-BOARD.kicad_pcb, 32-STEPPER-DRIVER-BOARD.kicad_sch]
2022-05-31 cleanup before DRC Errors
    [32-STEPPER-DRIVER-BOARD.kicad_pcb, 32-STEPPER-DRIVER-BOARD.kicad_sch, 8-STEPPER-DRIVER-CARD.kicad_pcb]
2022-06-03 Final checks for 32-stepper driver
    [32-STEPPER-DRIVER-BOARD.kicad_pcb]
2022-06-06 generate gerber for price check
    [32-STEPPER-DRIVER-BOARD-B_Cu.gbr, 32-STEPPER-DRIVER-BOARD-B_Mask.gbr, 32-STEPPER-DRIVER-BOARD-B_Paste.gbr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]
2022-06-09 final adjustments
    [32-STEPPER-DRIVER-BOARD.kicad_pcb, 32-STEPPER-DRIVER-BOARD.kicad_sch]
2022-06-09 32- driver board gerber generation
    [32-STEPPER-DRIVER-BOARD-B_Cu.gbr, 32-STEPPER-DRIVER-BOARD-B_Mask.gbr, 32-STEPPER-DRIVER-BOARD-B_Paste.gbr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]
2022-06-09 order placed
    [32-STEPPER-DRIVER-BOARD.kicad_pcb]
2022-06-10 64 motor initial setup
    [32-STEPPER-DRIVER-BOARD.kicad_pcb, 64-STEPPER-CONTROLLER.kicad_pcb, 64-STEPPER-CONTROLLER.kicad_sch]
2022-06-13 basic pin definitions added
2022-06-16 readme updates, 3d model paths updated
    [64_MOTOR_CONCEPTUAL.dwg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]
2022-06-16 readme updates
    [32-STEPPER-DRIVER-BOARD.kicad_pcb]
2022-06-17 update gitignore
    [Physical layout conceptual.dwg]
2022-06-17 Revert "update gitignore"
    This reverts commit 6e58a190580f49eac1285e80ab7aa617997ae66b.
    [Physical layout conceptual.dwg]
2022-06-17 Revert "Delete PCB/32-STEPPER-DRIVER-BOARD/32-STEPPER-DRIVER-BOARD-backups directory"
    This reverts commit 177caab1064322d9d7df6012cbe4820df753b896.
2022-06-17 Revert "Delete PCB/64-STEPPER-CONTROLLER/64-STEPPER-CONTROLLER-backups directory"
    This reverts commit f72b966d8d27d6964fcca2892ab00198c4950c66.
2022-06-17 Revert "Delete PCB/8-STEPPER-DRIVER-CARD/8-STEPPER-DRIVER-CARD-backups directory"
    This reverts commit 18a410249bb65aef49d1b6562cd3212f99cfb8d6.
2022-06-17 Creating classes
    [Physical layout conceptual.dwg]
2022-06-23 first successful motor spinning
2022-07-01 serial research and development
    [64_MOTOR_CONCEPTUAL.dwg, Auidio_Conversion_Flow.dwg, Physical layout conceptual.dwg]
2022-07-10 Finish design of main board
    [64-STEPPER-CONTROLLER.kicad_pcb]
2022-07-11 final changes to 64-pcb and testing renders
    [32-STEPPER-DRIVER-BOARD.kicad_pcb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]
2022-07-13 begin stepper wiring breakout board
    [2-STEPPER-BREAKOUT.kicad_pcb, 2-STEPPER-BREAKOUT.kicad_sch]
2022-07-14 Finish 2-motor breakout, submit order for 2 & 64
    [2-STEPPER-BREAKOUT-B_Cu.gbr, 2-STEPPER-BREAKOUT-B_Mask.gbr, 2-STEPPER-BREAKOUT-B_Paste.gbr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]
2022-07-20 64-stepper driver debugging
    [2-STEPPER-BREAKOUT.step]
2022-07-25 setup processing 3 and begin serial work
    [Auidio_Conversion_Flow.dwg, example_converted.csv]
2022-07-26 conceptual layout update
    [Physical layout conceptual.dwg]
2022-07-27 more work
    [Physical layout conceptual.dwg]
2022-08-01 serial driver progress
    [2-STEPPER-BREAKOUT.kicad_pcb, 2-STEPPER-BREAKOUT_MIR.step]
2022-08-08 midid tests
    [example_converted.csv]
2022-09-13 added matrix motor controls ground work
2022-10-13 fft tests
    [64-STEPPER-CONTROLLER.kicad_pcb]
2022-11-22 BGA general setup
    [64-STEPPER-CONTROLLER.kicad_pcb, 64-STEPPER-CONTROLLER.kicad_sch]
2022-12-19 Clean up serial print statements
2022-12-19 Create BOM for 32-Board
    [2-STEPPER-BREAKOUT.kicad_sch, 32-STEPPER-DRIVER-BOARD.csv, 32-STEPPER-DRIVER-BOARD.kicad_sch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]
2023-01-13 update documentation
    [Auidio_Conversion_Flow.dwg]
2024-01-17 Remove STM32 stuff
